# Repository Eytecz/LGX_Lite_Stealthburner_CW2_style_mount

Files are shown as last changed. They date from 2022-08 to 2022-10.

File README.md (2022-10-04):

# LGX_Lite_Stealthburner_CW2_style_mount
LGX Lite extruder mount for the Voron Stealthburner. The standard bowden clip delivered with the LGX Lite is to be removed, and a standard UM2 connector has to be inserted in the top printed part. This style clip is to be used: https://nl.aliexpress.com/item/32896103430.html. If you're lucky you might have some laying around already.

# LGX Lite mount ERCF
The ERCF version is made to accomodate the LGX Lite with the stealthburner and the new carriage, including the toolhead sensor as it is being used for the ERCF. The housing style is matching with the original CW2 design. I recommend to insert a 3mm long 4x2mm bowden tube on the bottom of the LGX Lite to guide the filament properly. The cover and cable carrier mount can be re-used from the original version. The top of the front body is made to insert the bowden tube until it reaches into the LGX Lite, through a standard bowden tube clip with retainer ring. A lever latch is designed to change the pretension on the filament. 

2022-08-10 21_20_59-Solid Edge 2022 - Assembly - LGX_Lite_Stealthburner_ERCF asm

The toolhead sensor is a standard hall effect switch (AH3364Q-P-B), which can be soldered to some wires with a connector. This sensor enters in between both halves of the support body and can be fixed using an angled M3x8 DIN912 bolt. Please be careful not to overtighten this bolt as it clamps directly onto the sensor housing. A standard washer M3 is to be inserted in the slot centered with the filament path. The magnet can be inserted in the front. Be sure to check the correct polarity.

To mount the LGX Lite to the body, use the 4 screws DIN912 M3x16mm, too long screws will damage the gears within the LGX!

Optionally one can choose to use the PCB version, which supports the Hartk Stealthburner PCB.

2022-10-04 20_12_45-Solid Edge 2022 - Assembly - LGX_Lite_Stealthburner_ERCF asm

# M3 Threaded insert locations
In the front housing there are 2 threaded inserts M3 which needs to be placed on the 'inside' to fixate the actual Stealthburner cover to. 

2022-08-10 21_23_19-Solid Edge 2022 - Assembly - LGX_Lite_Stealthburner_ERCF asm

In the rear housing there are 4 threaded inserts M3 to be placed on the back as shown in the image below.

2022-08-10 21_24_36-Solid Edge 2022 - Assembly - LGX_Lite_Stealthburner_ERCF asm

# Cable hatch and cable carrier

The standard cable door hatch and cable carrier support can be re-used from the original CW2. Be sure to mount the cable door before mounting the LGX Lite into the housing. You won't be able to reach the fastener once the LGX Lite is placed.

2022-08-10 21_26_32-Solid Edge 2022 - Assembly - LGX_Lite_Stealthburner_ERCF asm

Optional for the PCB version is the enlarged cover.

2022-10-04 20_12_10-Solid Edge 2022 - Assembly - LGX_Lite_Stealthburner_ERCF asm

I am not responsible in any way on how this impacts your printer. Use at your own risk.

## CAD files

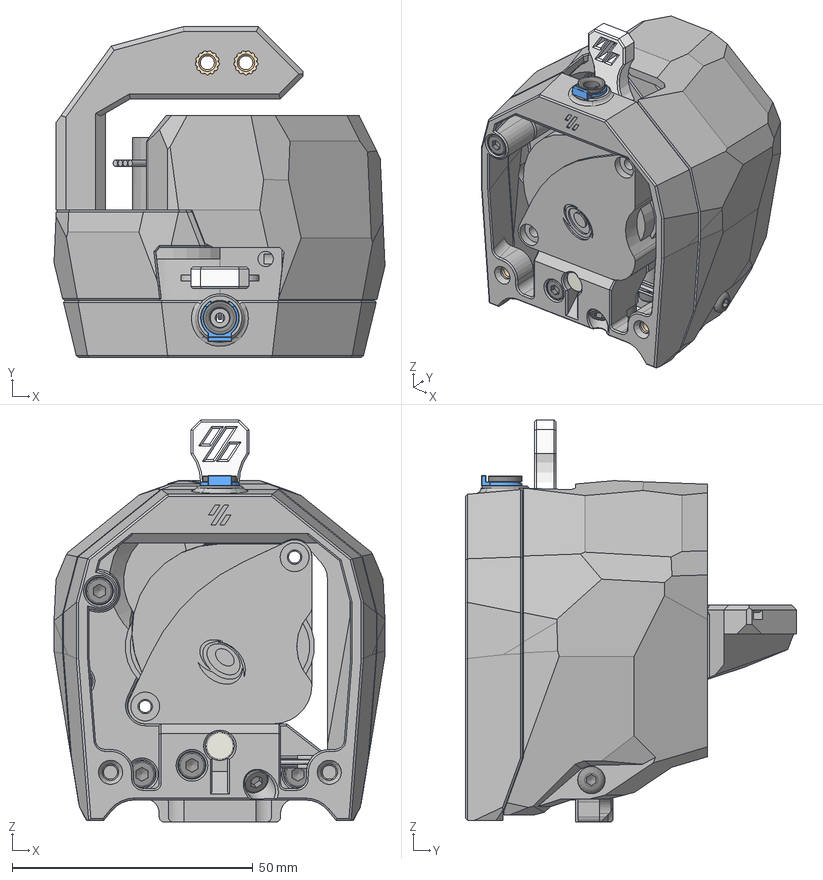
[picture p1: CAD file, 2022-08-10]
LGX_Lite_Stealthburner_ERCF/STEP/LGX_Lite_Stealthburner_ERCF_rev01.stp
68.7 x 68.6 x 83.4 mm
LGX-Lite Dummy
Front_body_LGX_Lite_Stealthburner_ERCF_Released_rev01
Rear_body_LGX_Lite_Stealthburner_ERCF_Released_rev01
[a]_Tension_rocker_LGX_Lite_Stealthburner_ERCF_rev01
Magnet6x3 v1
M3 THREADED INSERT x 9
AH3364Q-P-B v1
M3 Washer
Tube clip^E3D Revo 6
Circlip^E3D Revo 6
chain_anchor_2hole
cable_cover
ISO 7380-1 - M3 x 6
ISO 4762 - M3 x 10 x 2
ISO 4762 - M3 x 8 x 2
ISO 4762 - M3 x 25 x 2
ISO 4762 - M3 x 20
ISO 4762 - M3 x 16 x 4
ISO 4762 - M3 x 12

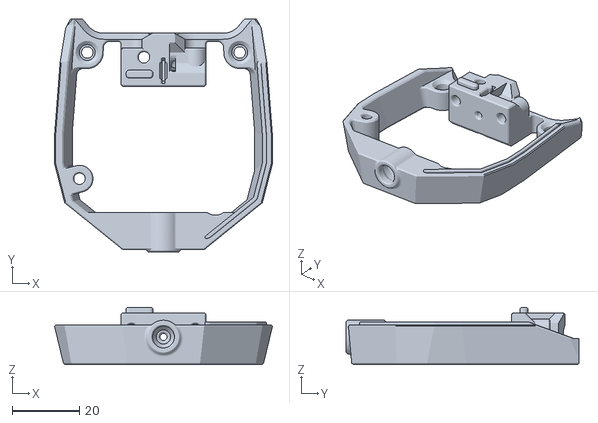
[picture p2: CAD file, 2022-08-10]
LGX_Lite_Stealthburner_ERCF/STL/Front_body_LGX_Lite_Stealthburner_ERCF_Released_rev01.stl
64.9 x 69.4 x 17.0

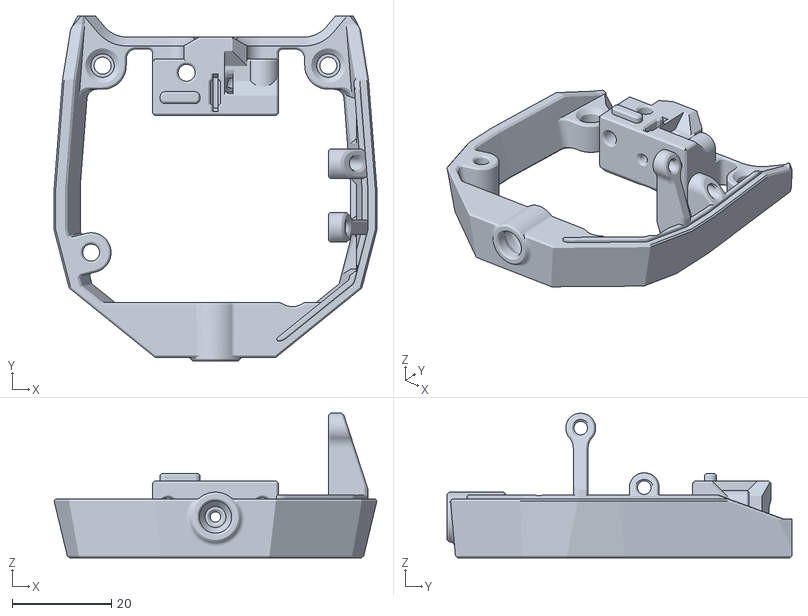
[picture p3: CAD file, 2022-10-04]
LGX_Lite_Stealthburner_ERCF_PCB/STL/Front_body_LGX_Lite_Stealthburner_ERCF_PCB_Released_rev01.stl
64.9 x 69.4 x 29.1

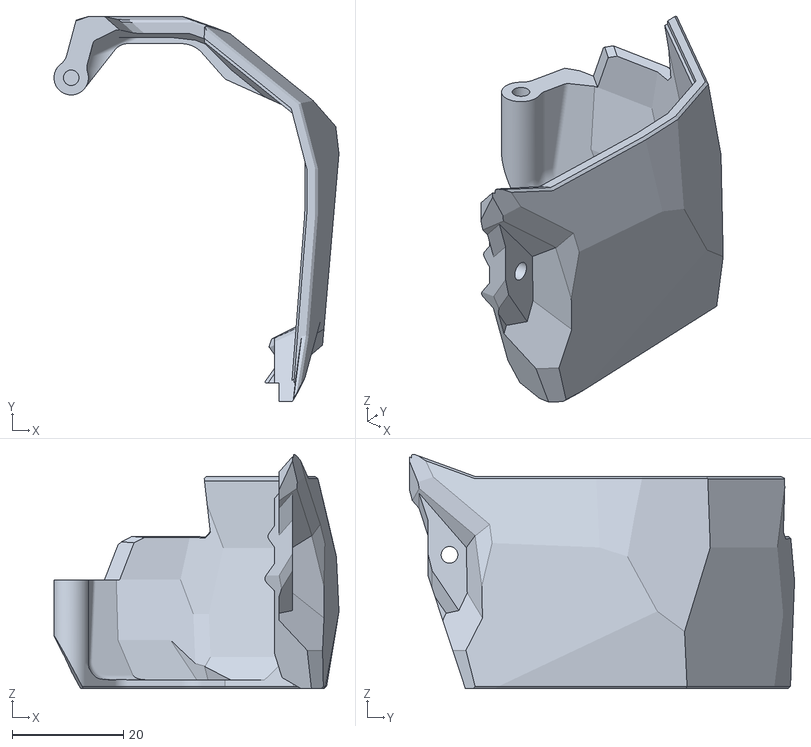
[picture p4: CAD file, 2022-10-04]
LGX_Lite_Stealthburner_ERCF_PCB/STL/Cable_cover_LGX_Lite_Stealthburner_PCB_Released_rev01.stl
51.3 x 69.4 x 42.2

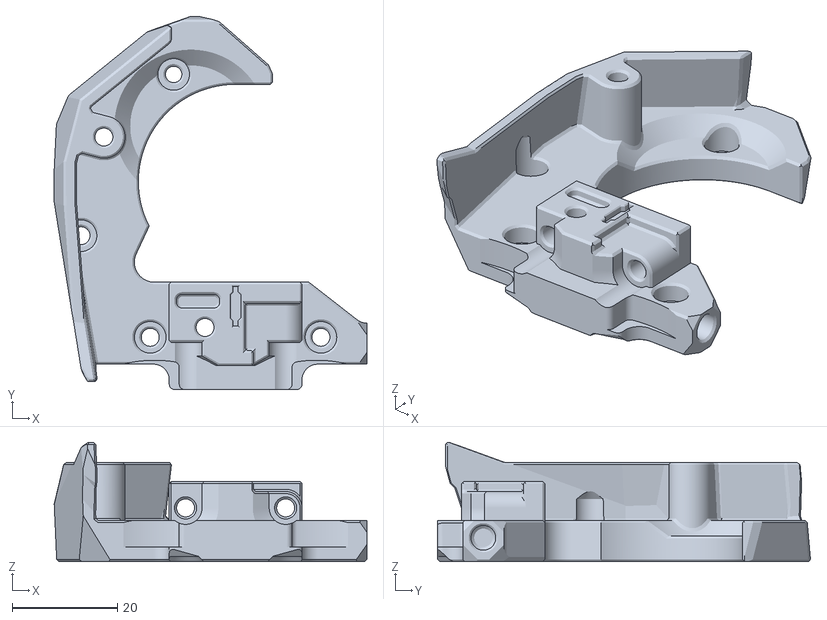
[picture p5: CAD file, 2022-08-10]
LGX_Lite_Stealthburner_ERCF_PCB/STL/Rear_body_LGX_Lite_Stealthburner_ERCF_Released_rev01.stl
59.3 x 70.8 x 22.6

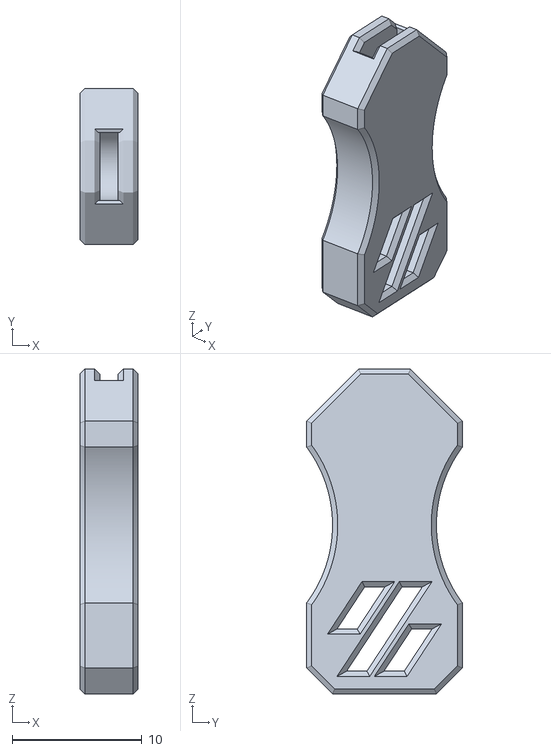
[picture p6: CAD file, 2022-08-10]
LGX_Lite_Stealthburner_ERCF_PCB/STL/[a]_Tension_rocker_LGX_Lite_Stealthburner_ERCF_rev01.stl
4.50 x 12.0 x 25.0

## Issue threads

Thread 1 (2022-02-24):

Screw locations

rlaferla, 2022-02-24:
Excellent mount but can you circle/show where the screws go?  Are there heat inserts too?

rlaferla, 2022-02-24:
3 out of the 4 screw locations.  Are these correct?  What about the 4th?

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

Eytecz, 2022-02-25:
Hi, this seems a bit odd. I believe your LGX is not properly positioned? According to the CAD it should align perfectly. Keep in mind that you do not need to use those 2 holes for fixing the LGX. They are placed there in case you'd like to remove the LGX motor without completely disassembling the body.

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

rlaferla, 2022-02-25:
I'm sorry but I don't understand your answer.   I think my LGX Lite is positioned properly but the lever is just not in the upright position.  How is your printed part fixed to the LGX Lite?  Do I need to replace the two long black screws on the front of the LGX Lite with longer ones that also attach your mount?  ie.  the upper right and lower right diagonal screw holes.

talmus-gibal, 2022-03-09:
If I'm understanding your question correctly, the LGX lite includes a pack of square M3 nuts. When you remove the front and back plates of the LGX lite you'll see a few slots around the perimeter of the main body which line up with the holes on the outside. Place four nuts on the bottom four slots then attach the two halves of the mount to the LGX lite.

rlaferla, 2022-03-21:
Sorry for the delay but I am in the midst of a major overhaul to CAN bus umbilical and LGX Lite.  Now I'm back to this issue.  What I need (and another user posted a comment on another issue that they also need it) is a diagram or photo that shows where the screws and heat inserts go.

An example would be this but just a simple photo where you marked the locations M3x12, heatinsert, etc... would suffice.  I know this seems obvious to you but we are asking because it's not obvious to us and we don't want to find out later that a screw was the wrong size or in the wrong location or needed a heat insert.

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

rlaferla, 2022-03-21:
Also, I reprinted the rear cover which fixed the alignment.  I may have used the wrong file initially.  I still need the screw types/length and heat insert locations

rlaferla, 2022-03-21:
a. Holes 2 and 3 are not flush.  I don't know if the whole back needs to be flush/flat or if this is ok.
b. Hole 1, does this need a heat insert?
c. What are the pair of holes at 4 and 6 for?
d. What is 5?

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

Closed 2022-02-25.

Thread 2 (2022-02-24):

Bowden lip

rlaferla, 2022-02-24:
It seems like we need to remove the Bowden lip to use this mount.  Is this true?  If so, do we re-insert it on the mount hole?

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

Eytecz, 2022-02-25:
Hi, the clip that it was designed for is a bit more rigid than the standard clip delivered with the LGX Lite. This style clip is to be used: https://nl.aliexpress.com/item/32896103430.html

And yes, you need to remove the clip in the LGX Lite itself. The bowden tube is fixed by the printed part a bit higher up.

It is mostly already delivered with a lot of hotends, you might already have one laying around :)

Closed 2022-02-25.

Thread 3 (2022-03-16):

UM2

rlaferla, 2022-03-16:
I cannot find these UM2 collets.  The ones on AliExpress are on a 2 month backorder.  Is there a way to redesign the part to use something more available?  Perhaps even the original LGX Lite one?  I have also tried two different types which involved shipping costs that were a multiple of the product.  It's not that I am not trying...

SvenBarracuda, 2022-03-18:
any chance to get a photo too see where all the brass m3 heatinserts goes? only can imagine 4 of your pics...dont want to rip apart my working SB on CW1 just to see that i missed something

rlaferla, 2022-03-21:
I filed an issue on the heat inserts and screws but it was closed.  We really need a diagram or photo like you said.

rlaferla, 2022-04-05:
I know believe this is a bug in the non-ECRF model.  The ECRF model has a hole for that fits the UM2 collet perfectly.  The non-ECRF version does not.  Please fix this.

Jaans, 2022-06-03:
Here are some photos of my assembly showing where I placed inserts (or at least where I think they should go):
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

Remember the side insert for closing the wire cover door.
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

Once assembled with motor:
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

Eytecz, 2022-08-13:
New design has been made, if more people have this issue a modification can be made.

Closed 2022-08-13.

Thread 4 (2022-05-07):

ERCF sensor triggering due to bolts

funkyskull, 2022-05-07:
This is a great design, but I ran into issues with the bolts on either side of the magnet.
When completely assembled the ERCF magnetic was constantly triggered.
After a bit of trouble-shooting I found that removing the two bolts resolved the issue.
Maybe consider removing those bolt holes or specing aluminum bolts, which might remove the effect?

 btw - I redesigned the front plate to use an ECAS fitting and it works great. Again thanks for the great design.

mattapperson, 2022-05-13:
Nice @funkyskull i was pulling my hair out having tested this pre-release and it worked and then ran into the always triggered issue post-release. Tried your suggestion and it seems to have fixed it! Must have failed to install those screws during testing 🤦‍♂️

mattapperson, 2022-06-01:
@funkyskull would you mind sharing your version?

Eytecz, 2022-08-13:
New design has been uploaded where this issue has been resolved.

Closed 2022-08-13.

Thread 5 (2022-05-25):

Extruder filament hole is slightly offset to the right

damiandudycz, 2022-05-25:
I don't know if it's due to some changes in the original parts design, but for some reason the extruder I slightly too far to the right (looking from the front). Would it be possible to adjust it to the newest parts?

ctilley83, 2022-06-26:
> I don't know if it's due to some changes in the original parts design, but for some reason the extruder I slightly too far to the right (looking from the front). Would it be possible to adjust it to the newest parts?

Were you able to fix this issue on your own? I'm worried about this myself.

Jaans, 2022-06-29:
FWIW, I printed a new set of CW2 and LGX Lite and it aligns perfectly. Not sure why yours is offset? How much is it - do you have a photo?

I did notice that the little square nuts of the LGX Lite has some movement in them to adjust, so maybe it's that ?

damiandudycz, 2022-07-04:
After measuring it in Fusion 360 - it was 0.2mm, nearly visible. But still. FYI - this issue was also present in original Stelathburner files, so I guess this is why it was moved here as well. I know 0.2mm is not a real issue, but just mentioning - it is there.

Jaans, 2022-07-04:
@damiandudycz Cool - good to know, and by how much

Eytecz, 2022-08-13:
New design has been uploaded where this issue has been resolved. However in the original Voron design this issue is still present.

Closed 2022-08-13.

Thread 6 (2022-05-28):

Please make Fusion 360 .f3d model available

Jaans, 2022-05-28:
This design is fantastic and has so much promise!
Thank you for sharing.

Would you be open to sharing the source CAD model, assuming it's a Fusion 360 .f3d model?
(The STEP files lack parametric history)

That would open it up to others to adapt it to the minor issues reported like:
- UM2 collet fitting only the sensor version
- ECAS fitting support (and other?)
- Potential alignment issue with filament hole
- Hall Effect Sensor issue with spaced bolts

Thanks again for this!

Eytecz, 2022-08-13:
I have made the STEP files available. The base design is not made in Fusion 360 but in Solid Edge, which means I can't make the f3d model available as it does not exist.

Jaans, 2022-08-13:
Awesome and thank you for doing this mod in the first place.

Closed 2022-08-13.

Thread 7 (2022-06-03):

Ercf Sensor not working

33martin, 2022-06-03:
has anyone managed to get the sensor to work?  my sensor switches perfectly outside the housing.  when i put it in it doesn't work (and yes the washer is magnetic)

33martin, 2022-06-09:
fixed my problem by using 2 magnets in a row.  I'll try modifying the cad file to put the magnet deeper into the case

Benoitone, 2022-06-09:
Your magnet may not be powerful enough. Maybe it's better that you find a more powerful magnet... If you modify to have the magnet closer to the washer you may have the opposite problem...

33martin, 2022-06-09:
I have tried various really strong neodyn magnets (the washer was also pulled strongly towards the magnet) but without success.  only when I used the second magnet it worked without any problems

Benoitone, 2022-06-09:
Do you really use AH3364Q-P-B hall sensor?

eamars, 2022-06-29:
I realized the hall effect sensor shouldn't be pushed all the way in otherwise it won't sense the change to the washer position. I suggest you to tune the position of the sensor first to see if that helps.

Jo3yDaPh1sH, 2022-07-02:
Stacking a second magnet worked for me.

Eytecz, 2022-08-13:
New design has been uploaded where this issue has been resolved. The fix was to remove the bolt on the sensor side going from the front to the back piece.

Closed 2022-08-13.

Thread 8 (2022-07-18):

Suggested Improvement, PTFE Tube 1 piece

lococnc, 2022-07-18:
Let the PTFE tube from the toolhead pass all the way up into the bottom receiver on the LGX Lite. I drilled it out to 4mm and this also ensures alignment of the filament path.
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

Eytecz, 2022-08-13:
Good modification, but is not relevant for the ERCF version, which is the only version I made available until now with the new design.

Closed 2022-08-13.

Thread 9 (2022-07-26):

Adapt to released CW2

KoeRt888, 2022-07-26:
Hi,
Is it possible for you to adjust the LGX Lite mount to the new CW2 specific hotend mounts?
With Stealthburner's release the CAD files are available [here](https://github.com/VoronDesign/Voron-Stealthburner)

dmnkhhn, 2022-07-30:
Did you identify any specific parts that need adjustments? I'm about to build the Stealthburner with the LGX Lite extruder and the Rapido hotend and a quick moving around of the parts in Fusion 360 (see attached file) it all looks quite good actually.
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

KoeRt888, 2022-08-01:
It all lines up well except for the gap between the toolhead an the front extruder plate. There is a 1mm gap where CW2 doesn't have one.
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

Cosmetically the toolhead has a new shape where but that isn't a big deal in my eyes:
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

Eytecz, 2022-08-13:
New design has been uploaded where this issue has been resolved.

Closed 2022-08-13.

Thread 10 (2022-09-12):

Plans for a non-ERCF version?

KoeRt888, 2022-09-12:
Hi,
I know you had a version without the ERCF sensor before.
Just wondering if you plan on releasing a non-ERCF version again?
If not could the current files be used without the ERCF sensor?

salbang, 2022-09-12:
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

IMHO, you can just use ercf version without having the sensors with no problem.

Eytecz, 2022-09-12:
> Hi, I know you had a version without the ERCF sensor before. Just wondering if you plan on releasing a non-ERCF version again? If not could the current files be used without the ERCF sensor?

Hi, yes I had one before. At the moment right now I do not have plans to make a non-ercf version as the ercf version can be used without the sensor.

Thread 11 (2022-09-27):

Need more motor clearance on Rear_Body

x4runnerGunnerx, 2022-09-27:
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

I think this radius around the motor needs another 1mm or so of clearance as it is rubbing on the motor and on the LGX lite body on the top causing it to flex out of shape slightly.

x4runnerGunnerx, 2022-09-27:
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

Eytecz, 2022-10-04:
Are there more cases with this issue? Haven't heard about it before. There is clearance in the CAD, which is based on the original LGX Lite CAD from Bondtech. If the issue persists for more people I"ll look into it.

Closed 2022-10-04.

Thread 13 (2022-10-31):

Note that all other toolhead PCBs are impossible to design for due to the width of the LGX Lite

ChaosBlades, 2022-10-31:
In order to save the time of anyone else that tries to get any of the other toolhead PCBs to work... you can't for the following reasons.

**2 piece Stealthburner PCB** - This will never work because the LGX Lite pushes the PCB out and there is no way to get the pins to align on the fan PCB. Pretty sure you couldn't even adjust the position of the fan mount PCB because then one of the mounting holes  would be inside the 5015 fan housing. The PCB and fan housing would need to be modified to move the connector over. You can't even design a custom LGX Lite case to move the PCB in because the gears are in the way.

**Afterburner PCB** - While this is possible on the CW2 (LDO has a bracket) this is almost impossible on the LGX mod for the same reason as the 2 piece Stealthburner PCB. I say almost because you might be able to do it but you would need to extend the entire outer housing including the door, CW2, and possibly fan shroud. Then create another bracket similar to the LDO one that mounts to the side of the LGX Lite. All of this effort isn't worth the ~$15 the correct PCB costs.

Jaans, 2022-10-31:
Thank you for the PSA!
I was looking at these and had wondered whether it was going to fit / align.

jvandervyver, 2022-10-31:
You can use the follow fan PCB: https://github.com/Ramalama2/Voron-2-Mods/tree/main/SB_LGXlitePCB/PCB
I'm using that with this LGX Lite mount and created slightly wider cable door, but it doesn't require a special StealthBurner

salbang, 2022-11-01:
Hi Yohan,
Thanks for your work and sharing.
Would the 2 piece version work with mellow sb2040 two piece canbus board?
It think the form factor is about the same as the hartic two piece PCB.

2022년 10월 31일 (월) 오후 6:54, Johan van der Vyver ***@***.***>님이
작성:

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

th3fallen, 2022-12-30:
@ChaosBlades im not sure i'd agree it is absolutely possible to mount the 2 part one with an lgx lite.. as i've done here.. i will be reprinting the front though since it now has mounting holes which will be nice.
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

Jaans, 2022-12-31:
@th3fallen Thanks for the pictures and feedback. Looking good with TAP too ;-) 👍

Would you be up to sharing _exactly_ which parts / mounts you did use with the specific links?
The reason I'm asking for specific links, is that I've previously printed the Eytecz one from this repo and it didn't have the "mounts" for the hartk PCB:
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
Also, it had a section of plastic going right down the middle.

So I'm starting to think there are different STLs (revisions maybe) that work for some and not for others, depending on what they do.

The indicated "mounts" for the HartK PCB board seems to be for either an old version of the board or a non 2pc-stealthburner version that I haven't seen before:
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

Despite all this, your images show the 2PC PCB hartk board for Stealth Burner that I know (and have lying around). I don't know how you managed to get this fitted given the above screenshot showing 3 separate JST connectors. If I try to position the SB PCB, I cannot get the 2x4 (8Pin) header to fit between the plastic PCB mounts.

Am I maybe missing something entirely here?

th3fallen, 2022-12-31:
@Jaans oh no I don’t have it mounted with his new front yet I’m actually modding the cad now I’ll share when it works. I was attempting to show that it’s not impressive as the title leads you to believe

th3fallen, 2022-12-31:
@Jaans here is the first modified version it works, but i want to shift the board up about a mm https://p181.p1.n0.cdn.getcloudapp.com/items/7KujEnwe/8030095d-fbfb-4a86-a0c1-8ef56562f6ae.stl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

LAP87, 2023-02-02:
I am about to do CAN overhaul, do you think you will do a version that incorporates EBB36 / EBB42?

helman, 2023-08-30:
@th3fallen is the mod support fly-sb2040? I'm using this mod at the moment https://www.printables.com/model/348581-voron-stealthburner-lgx-lite-mellow-sb2040 , but soon will need the filament sensor for ercf.

akonkol, 2023-08-30:
> I am about to do CAN overhaul, do you think you will do a version that incorporates EBB36 / EBB42?

this might be interesting to you: https://github.com/BondtechAB/Voron/tree/main/Voron_2.4-VT-SW/LGX_lite/STL/SB-LGX_lite-Ebb36

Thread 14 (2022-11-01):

Front Body Magnet Hole likes to print in thin air. I fixed it.

ChaosBlades, 2022-11-01:
**Original:**
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
**Fix:**
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
I cut some 0.1 mm sides into the bridge so it didn't try to print a right angle in thin air. Then it tried to print the first bridge in 2 parts because the bridges were in between 2 layers with a 0.2 mm layer height. So I moved the floor of the hole up by 0.1 mm then removed the cross bridge because it is unnecessary. If you notice the cross bridge does not even get printed in the original file. This is because of the bridge being in between a layer like mentioned before.
[Front_body Step and 3MF.zip](https://github.com/Eytecz/LGX_Lite_Stealthburner_CW2_style_mount/files/9913324/Front_body.Step.and.3MF.zip)

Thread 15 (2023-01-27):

Not an Issue, but a question.

32368734, 2023-01-27:
Do you think this is going to work with a SB2040 pcb?

BigBadLoser, 2023-01-27:
It doesn't work with CAN boards

32368734, 2023-01-27:
Thanks for you answer. Do you know if there are other options for stealthburner in combination with lgx lite and canbus?

BigBadLoser, 2023-01-27:
There are toolheads that fit EBB36, I know bondtechs new official LGX Lite mount works for EBB36. I hope someone figures out a solution for sb2040 and sb2240 soon, would love to use them with my LGX Lite.

Closed 2023-01-28.

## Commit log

2022-02-09 Initial upload
    [Front_body_LGX_Lite_Stealthburner_ERCF_rev04.stl, Front_body_LGX_Lite_Stealthburner_rev02.stl, Rear_body_LGX_Lite_Stealthburner_ERCF_rev01.stl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]
2022-08-10 Updated version with released CAD
    Version is based on actual CAD files from the released stealthburner/clockwork 2 parts and fit on the new toolhead carriage.
    Several improvements were made:
    - Front is now completely opened up, to allow for access to the extruder gears while leaving the sub-assembly mounted to the carriage.
    - ERCF sensor triggering issue is resolved by removing the bolt on the side of the hall effect sensor.
    - Filament path offset (0.2mm) is removed and this version is completely symmetric in the location of the filament path, in contrary to the official version.
    The non-ercf version is not added as the hall sensor can be left out in case a toolhead sensor is not desired.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
    [Front_body_LGX_Lite_Stealthburner_ERCF_Released_rev01.stl, Front_body_LGX_Lite_Stealthburner_ERCF_rev04.stl, Front_body_LGX_Lite_Stealthburner_rev02.stl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]
2022-10-04 PCB option added
    Added CAD files for the original Hartk Stealthburner PCB, which support it using the LGX Lite mount.
    [Cable_cover_LGX_Lite_Stealthburner_PCB_Released_rev01.stl, Front_body_LGX_Lite_Stealthburner_ERCF_PCB_Released_rev01.stl, Rear_body_LGX_Lite_Stealthburner_ERCF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]
2022-10-04 Update README.md
    PCB option added.
